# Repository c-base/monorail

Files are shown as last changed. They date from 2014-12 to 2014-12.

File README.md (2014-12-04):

monorail
========

Designfiles for Hardware and Electronics of the c-base monorail

#### Legende Dateinamen

Lo = Lokomotive (Traktionswagen)  
Kw = Kontrollwagen (Akku, Intelligenz..)  
Fw= Flaschenwagen  

Typ A# = Spant (Quer zur Fahrtrichtung, vertikal)  
Typ I# = Stringer (Längs zur Fahrtrichtung, paralell zur Schiene, vertikal oder schräg)  
Typ D# = Deck (Längs zur Fahrtrichtung, paralell zur Schiene, horizontale Oberfläche, Deck-ähnlich)  
Typ V# = Verstärkung / Aussteiffung  
Typ E# = Montagekomponente für Elektroteile  

lower caps u = "und" --> mehrere Komponenten in einer Datei

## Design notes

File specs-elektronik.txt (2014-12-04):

Anforderungen Elektronik Monorail

Modul "Abstand"
benötigt: pro Zug zwei
Anschlüsse:
	2x Bumper (links und rechts)
	1x IR-Distanz-sensor (sharp)
	1x RGB-LED (nicht extrem hell, aber auch keine müde funzel/kontroll-LED
	Bus
Stromversorgung vom Spannungsregler auf dem Akkucontrol-board

Modul "Motortreiber"
benötigt: pro Zug einen
	Anschluss des fertigen Motortreibers
	Bus
Stromversorgung vom Spannungsregler auf dem Akkucontrolboard
Motorstromversorgung direkt vom Akku mit vielen Volts

Modul "Akkucontrol"
benötigt: pro Zug einen
Anschlüsse:
	Akkustrom
	Ladestrom
	Balancerkontakte
	Bus
Funktionen:
	Laden und Balancen des Akkus
	Versorgung der Komponenten mit Strom in passender Spannung
		Bus-Strom: 3,3V
		Beagle bone black: 5V (vermutung!)
	Bereitstellung von Informationen über den Füllstand des Akkus über den Bus
	
Modul "Barcodescanner"
benötigt: pro Zug einen
Anschlüsse:
	IR-LED
	1-2 IR-Rx
	Bus
Stromversorgung vom Spannungsregler auf dem Akkucontrolboard
	
Modul "Flaschenwagen"
benötigt ersma gar nich, aber später pro Zug einen oder zwei
Anschlüsse:
	Modellbauservo oder kleiner Schrittmotor
	Lichtschranke oder Taster zum feststellen ob beladen oder leer
	LCD Display (zwei zeilen, z.b: http://www.watterott.com/de/Serial-Enabled-16x2-LCD-Yellow-on-Blue-5V
		dient zur Anzeige für wen die Ladung bestimmt ist, bzw was eingeladen werden soll durch den Barbot
	Bus
Stromversorgung direkt vom Akku für den Servo (7,5V). Der Mikrocontroller könnte entweder seinen eigenen Spannungsregler haben oder aber vom Akkucontrolboard mit versorgt werden
		
Modul "Lichtwagen"
benötigt: ersma gar nich, aber später irgendwann pro lichtzug einen
Anschlüsse:
	zwei Modellbauservos für X und Y Ausrichtung
	PWM-Steuerung für sehr starke LEDs (Strahler!)
	PWM-Steuerung für nen paar dekorative RGB-LEDs rund um den Lichtwagen
	Bus
Stromversorgung direkt vom Akku für die Servos und die Highpower-LEDs mit eigenem Spannungsregler. Der Mikrocontroller könnte entweder seinen eigenen Spannungsregler haben oder aber vom Akkucontrolboard mit versorgt werden
	
Modul "Kamerawagen"
benötigt: ersma gar nich, aber später irgendwann pro kamerazug einen
Anschlüsse:
	zwei Modellbauservos für X und Y Ausrichtung
	Stromversorgung für Kamera
	vll. remotesteuerung der kamera
	USB-Verbindung zum Beagleboneblack
Stromversorgung direkt vom Akku für den Kamerastrom mit Spannungsregler. Der Mikrocontroller könnte entweder seinen eigenen Spannungsregler haben oder aber vom Akkucontrolboard mit versorgt werden

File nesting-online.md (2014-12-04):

# Online Nesting Services

"Nesting" ist das automatisierte Anordnen von Formen auf 2D-Flächen zwecks maschineller Bearbeitung. Ein Lasercutter oder Wasserstrahljet soll möglichst wenig Verschnitt erzeugen und seine maximale Bearbeitungsfläche optimal ausnutzen. Nesting-Software erzeugt und optimiert die Anordnung vieler verschiedener Einzeilteile auf einer Fläche unter Berücksichtigung der benötigten Stückzahlen aller Einzelkomponenten.  

Nestingsoftware ist teuer, aber inzwischen gibt es auch Nesting-Dienstleister "in der Cloud". Hier sind zwei:

##### Nesting Online:  
http://www.e-nesting.com  
http://www.mynesting.com/

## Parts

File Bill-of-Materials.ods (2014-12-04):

BOM Monorail |  |  |  |  |  |  |  |  |  |  |  | Wegertseder Shop-Code: 645646-361
Name | Produktname | Bezeichnung | Abmessung | Stck/Gebinde | benötigte Menge | Gebindepreis | Einzelpreis | Gesamtpreis | Gebindemenge | Gebindegesamtpreis | alternativ shop mögl | ShopLink | Datenblatt | Anzahl übrig
Laufräder | Kugellager | FAG Rillenkugellager 626-2Z | 6x19x6 mm | 1 | 10 | 3,29 € | 3,29 € | 32,90 € | 10 | 32,90 € | nein | https://zahnriemen24.de/artikel_FAG-Rillenkugellager-626-2Z-6x19x6-mm__16_6_193 |  | 0
Radachse | Schraube | Zylinderschraube mit Innensechskant DIN 912 | 6x25mm | 20 | 12 | 2,45 € | 0,12 € | 1,47 € | 1 | 2,45 € | ja | Wegertseder 2534-430 |  | 8
Kupplung | Schraube | Zylinderschraube mit Innensechskant DIN 912 | 6x25 | 20 | 12 | 2,57 € | 0,13 € | 1,54 € | 1 | 2,57 € | ja | Wegertseder 2534-430 |  | 8
Verbindungschraube | Schraube | DIN 912 M6x 30 | 6x30 | 20 | 1 | 2,45 € | 0,12 € | 0,12 € | 1 | 2,45 € | ja | Wegertseder 2534-432 |  | 19
U-scheiben radlager | U-scheibe | DIN125 M6 U-Scheibe | 12x1,6 | 100 | 36 | 2,21 € | 0,02 € | 0,80 € | 1 | 2,21 € | ja | Wegertseder 1498-302 |  | 64
Radmutter | Mutter M6 | Selbstsichernde Mutter DIN 985 A2 M6 | 11,05x6mm | 100 | 12 | 3,47 € | 0,03 € | 0,42 € | 1 | 3,47 € | ja | Wegertseder 3346-238 |  | 88
Motor | NEMA17 | NEMA 17
Motormutter | Mutter | DIN125 M3 U-Scheibe |  | 200 | 10 | 2,14 € | 0,01 € | 0,11 € | 1 | 2,14 € | ja | Wegertseder 1498-294 |  | 190
Motorschrauben | M3x10 | DIN 6912 M3X10 |  | 25 | 6 | 1,84 € | 0,07 € | 0,44 € | 1 | 1,84 € | ja | Wegertseder 2534-280 |  | 19
IR-Sensor-Schraube | M3x30 | DIN912 M3 30mm | M3x30 | 25 | 4 | 3,14 € | 0,13 € | 0,50 € | 1 | 3,14 € | ja | Wegertseder 2534-296 |  | 21
IR-Sensor-Mutter | M3 | DIN985 A2 M3 |  | 100 | 4 | 3,45 € | 0,03 € | 0,14 € | 1 | 3,45 € | ja | Wegertseder 3346-232 |  | 96
Antriebslager | Kugellager | FAG Rillenkugellager 625-2Z (5x16x5 mm) | 5x16x5 mm | 1 | 6 | 3,39 € | 3,39 € | 20,34 € | 6 | 20,34 € | nein | https://zahnriemen24.de/artikel_FAG-Rillenkugellager-625-2Z-5x16x5-mm__16_6_191 |  | 0
Antriebsachse | Metallstange | Metallstange 5mm Durchmesser, 95mm länge | 5x95mm |  | 1 |  |  |  |  |  |  | Qshell
Antriebsrad |  | Druckteil Fablab
Zahnscheibe Motorachse |  | Zahnscheibe AL 16 T2,5/18-2 |  | 1 | 1 | 10,60 € | 10,60 € | 10,60 € | 1 | 10,60 € | nein | https://zahnriemen24.de/artikelno_10_1_835 |  | 0
Zahnscheibe Antriebsachse |  | Zahnscheibe AL 16 T2,5/36-2 |  | 1 | 1 | 12,05 € | 12,05 € | 12,05 € | 1 | 12,05 € | nein | https://zahnriemen24.de/artikel_Zahnscheibe-AL-16-T2,5-36-2__10_1_845 |  | 0
Antriebsriemen | Zahnriemen, geschlossen | PU-Zahnriemen 6-T2,5-200 | 200mmx6mm | 1 | 1 | 11,55 € | 11,55 € | 11,55 € | 1 | 11,55 € | nein | https://zahnriemen24.de/artikel_PU-Zahnriemen-6-T2,5-200__2_4_4863 |  | 0
Drehgestellgelenk | Gelenkkopf | Gelenkkopf mit Innengewinde M3 |  | 1 | 3 | 13,25 € | 13,25 € | 39,75 € | 3 | 39,75 € | jein | http://www.conrad.de/ce/de/product/216429/Gelenkkopf-mit-Innengewinde-M3-Stahl?ref=searchDetail | http://www.produktinfo.conrad.com/datenblaetter/200000-224999/216429-da-01-de-Gelenk_Gis_3.pdf | 0
Elektronik
Hauptcomputer | Beagle Bone Black |  | 88.98mm x 54.63mm x 18.84mm | 1 | 1 | 45,00 € | 45,00 € | 45,00 € | 1 | 45,00 € | nein | http://www.watterott.com/de/BeagleBone-Black |  | 0
Abstandssensor |  | Sharp GP2Y0A21YK0F |  | 1 | 2 | 9,15 € | 9,15 € | 18,30 € | 2 | 18,30 € | nein | http://www.watterott.com/de/Sharp-GP2Y0A21YK0F | http://www.watterott.com/index.php?page=product&info=995&dl_media=1326 | 0
Notstop-Bumper | Schnappschalter | Schnappschalter, 5A-250V~ Wechsler, Lötan. | 19,8x6,4x15,0 | 1 | 4 | 2,50 € | 2,50 € | 10,00 € | 4 | 10,00 € | nein | http://www.reichelt.de/Schnappschalter-Endschalter/MAR-1050-5202/3/index.html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 | http://www.reichelt.de/index.html?ACTION=7&LA=3&OPEN=0&INDEX=0 | 0
Motortreiber |  | DRV8825 Schrittmotortreiber (High Current) |  | 1 | 1 | 13,28 € | 13,28 € | 13,28 € | 1 | 13,28 € | ja | http://www.watterott.com/de/DRV8825-Stepper-Motor-Driver-Carrier-High-Current | http://www.pololu.com/file/download/drv8825.pdf?file_id=0J590 | 0
Laderaumantrieb | Turnigy TGY-4805 | Turnigy TGY-4805-1.5PA Sail Winch Servo (Drum Type) | Size: 40.3 x 20.3 x 38.7mm | 1 | 1 | 8,28 € | 8,28 € | 8,28 € | 1 | 8,28 € |  | http://www.hobbyking.com/hobbyking/store/__42638__Turnigy_TGY_4805_1_5PA_Sail_Winch_Servo_Drum_Type_.html | http://84.200.30.165/cosmoshop/lshopimage/a/HIT-112081/zn1/HIT-112081_n1.jpg | 0
Laderaumverriegelung | Micro-Servo | HKSCM12-5 Single Chip Digital Servo (5V) 10g / 1.5kg / 0.18s |  | 1 | 2 | 2,91 € | 2,91 € | 5,82 € | 2 | 5,82 € | ja | http://www.hobbyking.com/hobbyking/store/__16261__HKSCM12_5_Single_Chip_Digital_Servo_5V_10g_1_5kg_0_18s.html | http://www.produktinfo.conrad.com/datenblaetter/500000-524999/507765-da-01-de-HUBMAGNET_HMB_1513_001_12VDC.pdf | 0
Akku |  | SLS XTRON 3200mAh 4S1P 14,8V 20C/40C | LxBxH 138x43x26mm | 1 | 1 | 33,99 € | 33,99 € | 33,99 € | 1 | 33,99 € | ja | http://www.stefansliposhop.de/liposhop/SLS-XTRON/SLS-XTRON-20C/SLS-XTRON-3200mAh-4S1P-14-8V-20C-40C::978.html |  | 0
Display |  | ST7565 Positive GLCD (128x64) with RGB backlight |  | 1 | 1 | 17,09 € | 17,09 € | 17,09 € | 1 | 17,09 € |  | http://www.watterott.com/de/ST7565-Positive-GLCD-128x64-with-RGB-backlight
Werkzeug und Schienen
Blindnietmutterzange |  |  |  | 1 | 1 | 27,99 € | 27,99 € | 27,99 € | 1 | 27,99 € | ja | http://www.amazon.de/Nietmaschine-Nietmuttern-Popnietzange-Nietzange-Einnietmutter/dp/B00A0280H8 |  | 0
Blindnietmutter |  | alu nietmutter m3x0,5 |  | 100 | 100 | 13,99 € | 0,14 € | 13,99 € | 1 | 13,99 € | ja | http://www.amazon.de/stk-Alu-Nietmutter-Nietmuttern-Blindnietmuttern/dp/B00AY01JXS |  | 0
rohrbiegegerät |  |  |  | 1 | 1 | 44,99 € | 44,99 € | 44,99 € | 1 | 44,99 € | ja | http://www.amazon.de/Hand-Rohrbieger-Rohre-Rohrbiegegerät-Kupfer-Bieger/dp/B00BIWCMKU |  | 0
Muttern |  | DIN 985 M3 A2 |  | 100 | 100 | 2,00 € | 0,02 € | 2,00 € | 1 | 2,00 € | ja | http://www.amazon.de/100-Stück-Edelstahl-Sechskantmuttern-selbstsichernd/dp/B004QV5EOQ |  | 0
Gewindestange |  | M3 x 1000mm V2A DIN975 | 3x1000 | 1 | 2 | 1,50 € | 1,50 € | 3,00 € | 2 | 3,00 € | ja | http://www.amazon.de/Stück-1000mm-Edelstahl-V2A-Gewindestange/dp/B004YE8ASW |  | 0
SchienenBohrer |  | Ironside 230114 HSS-Bohrer 5,0mm 2St.G DIN338 RN-geschliffen | 5mm | 2 | 2 | 4,85 € | 2,43 € | 4,85 € | 1 | 4,85 € | ja | http://www.amazon.de/Ironside-230114-HSS-Bohrer-DIN338-RN-geschliffen/dp/B0001E36I8?s=diy |  | 0
Schiene |  | 22 x 1 mm 2,5 m | 22x1x2500mm | 2,5 | 5 | 13,50 € | 5,40 € | 27,00 € | 2 | 27,00 € |  | http://www.hornbach.de/shop/Kupferrohr-als-Stange-22-x-1-mm-2-5-m/1318872/artikel.html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 |  | 0
Zahnriemen |  | Zahnriemen 10 -T10 - 3000 - offen - kevlar | 3000mm lang 10mm breit | 3 | 1 | 21,40 € | 7,13 € | 7,13 € | 1 | 21,40 € |  |  |  | 2
 |  |  |  |  |  |  |  | Gesamtpreis |  | Gebindegesamtpreis
SUMME |  |  |  |  |  |  |  | 415,44 € |  | 447,89 €
 |  |  |  |  |  |  |  |  |  | Preis für das zweite Fahrzeug
 |  |  |  |  |  |  |  |  |  | 280,42 €
 |  |  |  |  | Schienenpreis
 |  |  |  |  | Breite holzbalken |  |  | 30
 |  |  |  |  | höhe holzbalken |  |  | 40
 |  |  |  |  | Montageabstand |  |  | 25
 |  |  |  |  | Zugabe länge |  |  | 15
 |  |  |  |  | abstand zw halterung |  |  | 500
 |  |  |  |  | Länge Gewindestange |  |  | 80
 |  |  |  |  | Bedarf pro Meter |  |  | 160
 |  |  |  |  | Kosten Gewindestange |  |  | 0,24 €
 |  |  |  |  | Menge Muttern pro Meter |  |  | 6 | 0,21 €
 |  |  |  |  | Menge U-Scheiben pro Meter |  |  | 6 | 0,06 €
 |  |  |  |  | Kosten pro Meter |  |  | 5,91 €
 |  |  |  |  | Kosten pro Meter mit zahnschiene |  |  | 13,04 €

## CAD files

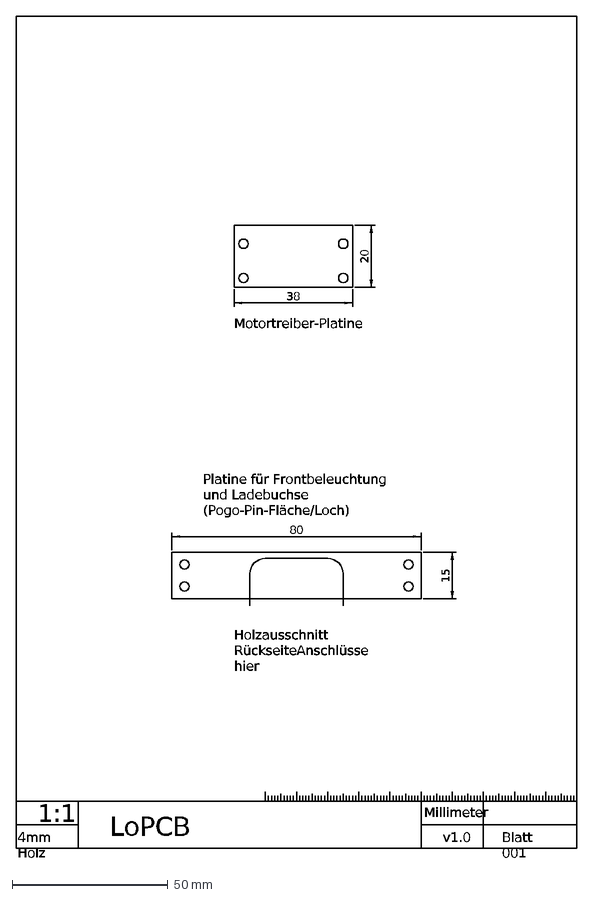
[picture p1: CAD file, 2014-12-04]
LoPCB.dxf
1:1
4mm Holz
Blatt 001
v1.0
Millimeter
Platine für Frontbeleuchtung und Ladebuchse (Pogo-Pin-Fläche/Loch)
Holzausschnitt Rückseite Anschlüsse hier
Motortreiber-Platine
LoPCB
38
20
80
15

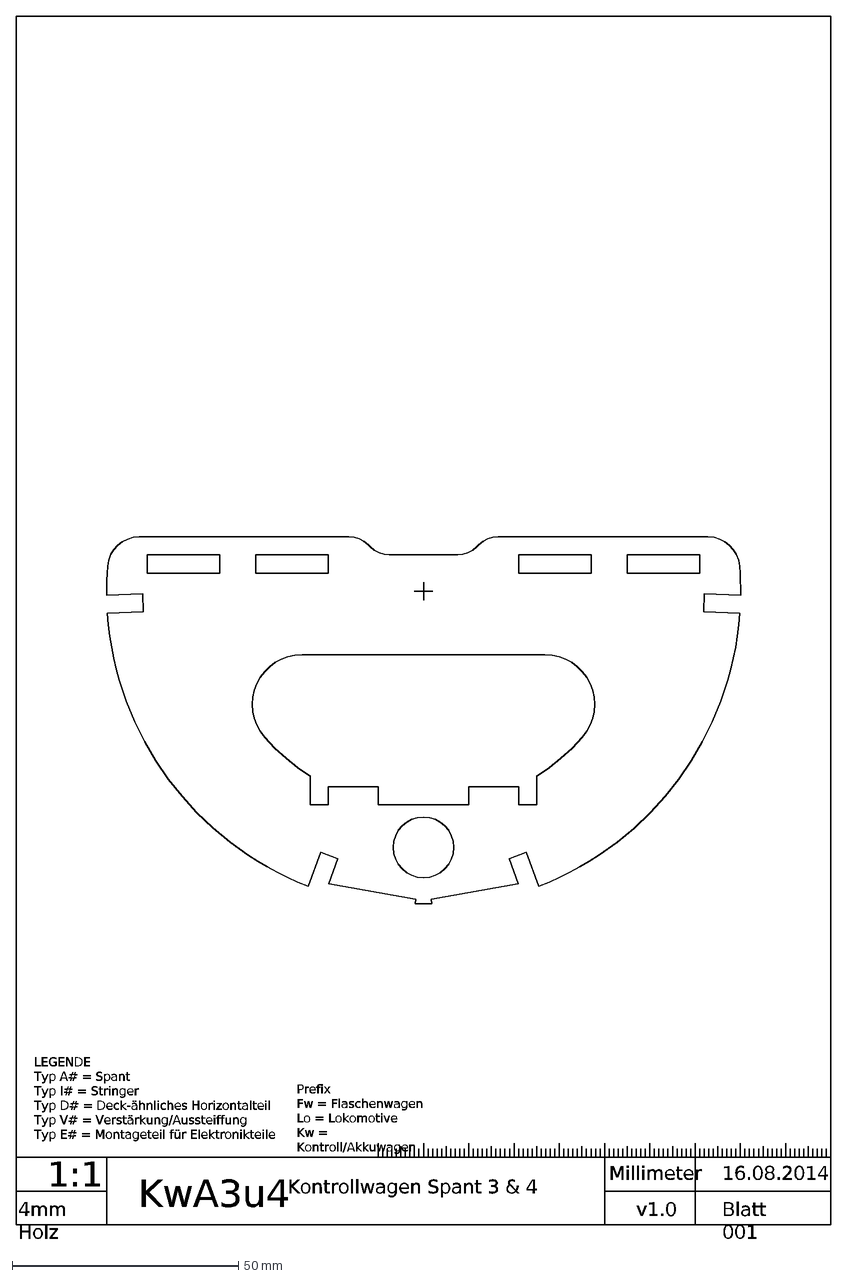
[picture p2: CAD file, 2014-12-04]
KwA3u4.dxf
1:1
4mm Holz
16.08.2014
Blatt 001
v1.0
Millimeter
LEGENDE Typ A# = Spant Typ I# = Stringer Typ D# = Deck-ähnliches Horizontalteil Typ V# = Verstärkung/Aussteiffung Typ E# = Montageteil für Elektronikteile
Prefix Fw = Flaschenwagen Lo = Lokomotive Kw = Kontroll/Akkuwagen
Kontrollwagen Spant 3 & 4
KwA3u4

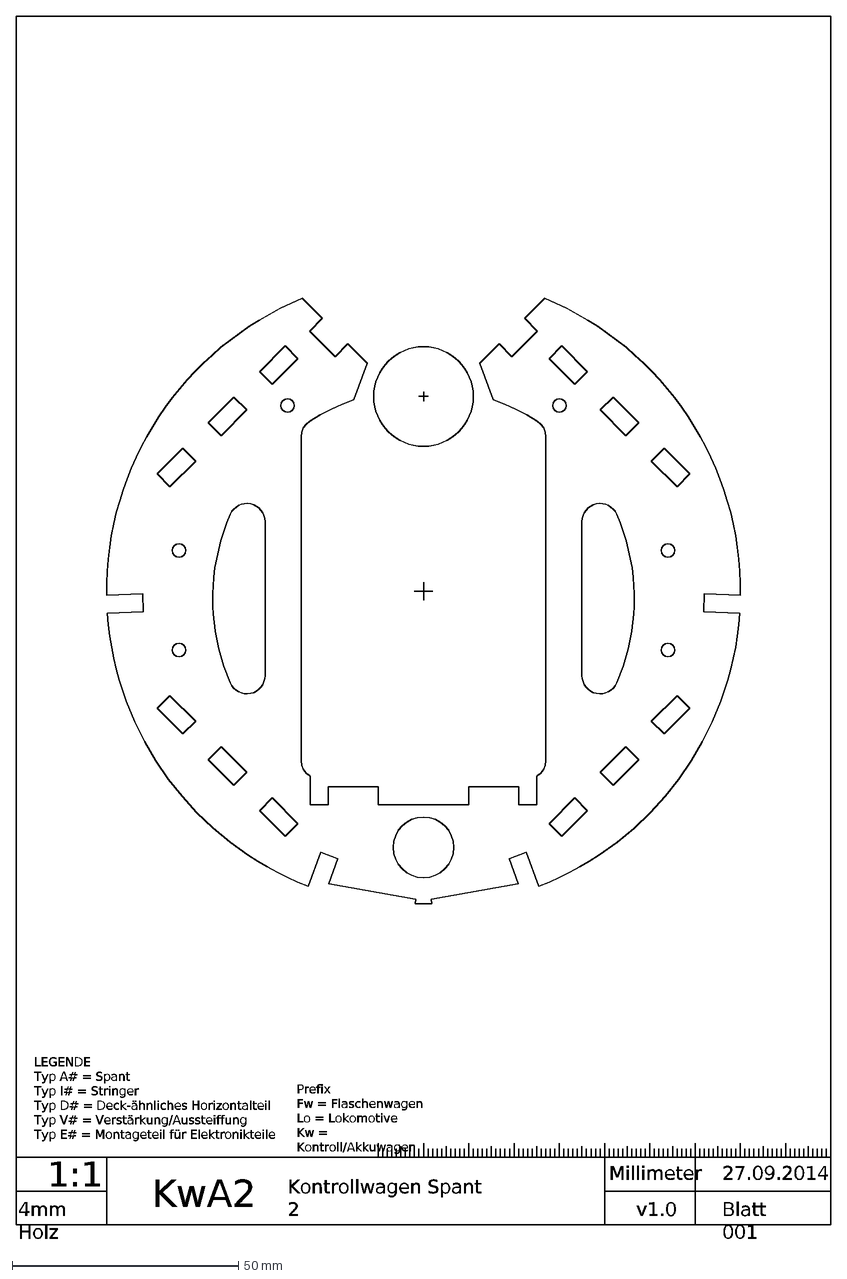
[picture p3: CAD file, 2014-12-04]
KwA2.dxf
1:1
4mm Holz
Blatt 001
v1.0
Millimeter
LEGENDE Typ A# = Spant Typ I# = Stringer Typ D# = Deck-ähnliches Horizontalteil Typ V# = Verstärkung/Aussteiffung Typ E# = Montageteil für Elektronikteile
Prefix Fw = Flaschenwagen Lo = Lokomotive Kw = Kontroll/Akkuwagen
KwA2
Kontrollwagen Spant 2
27.09.2014

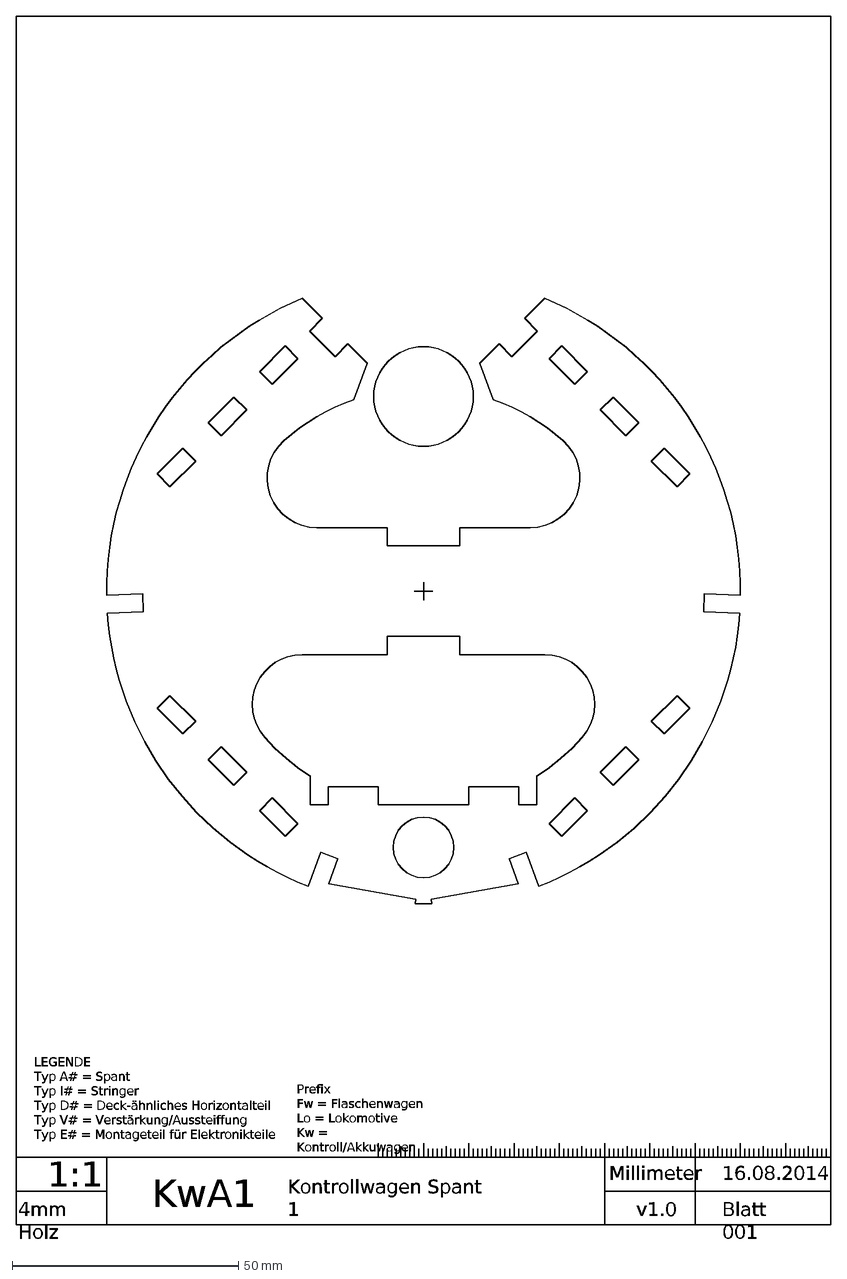
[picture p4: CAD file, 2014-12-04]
KwA1.dxf
1:1
4mm Holz
16.08.2014
Blatt 001
v1.0
Millimeter
LEGENDE Typ A# = Spant Typ I# = Stringer Typ D# = Deck-ähnliches Horizontalteil Typ V# = Verstärkung/Aussteiffung Typ E# = Montageteil für Elektronikteile
Prefix Fw = Flaschenwagen Lo = Lokomotive Kw = Kontroll/Akkuwagen
KwA1
Kontrollwagen Spant 1

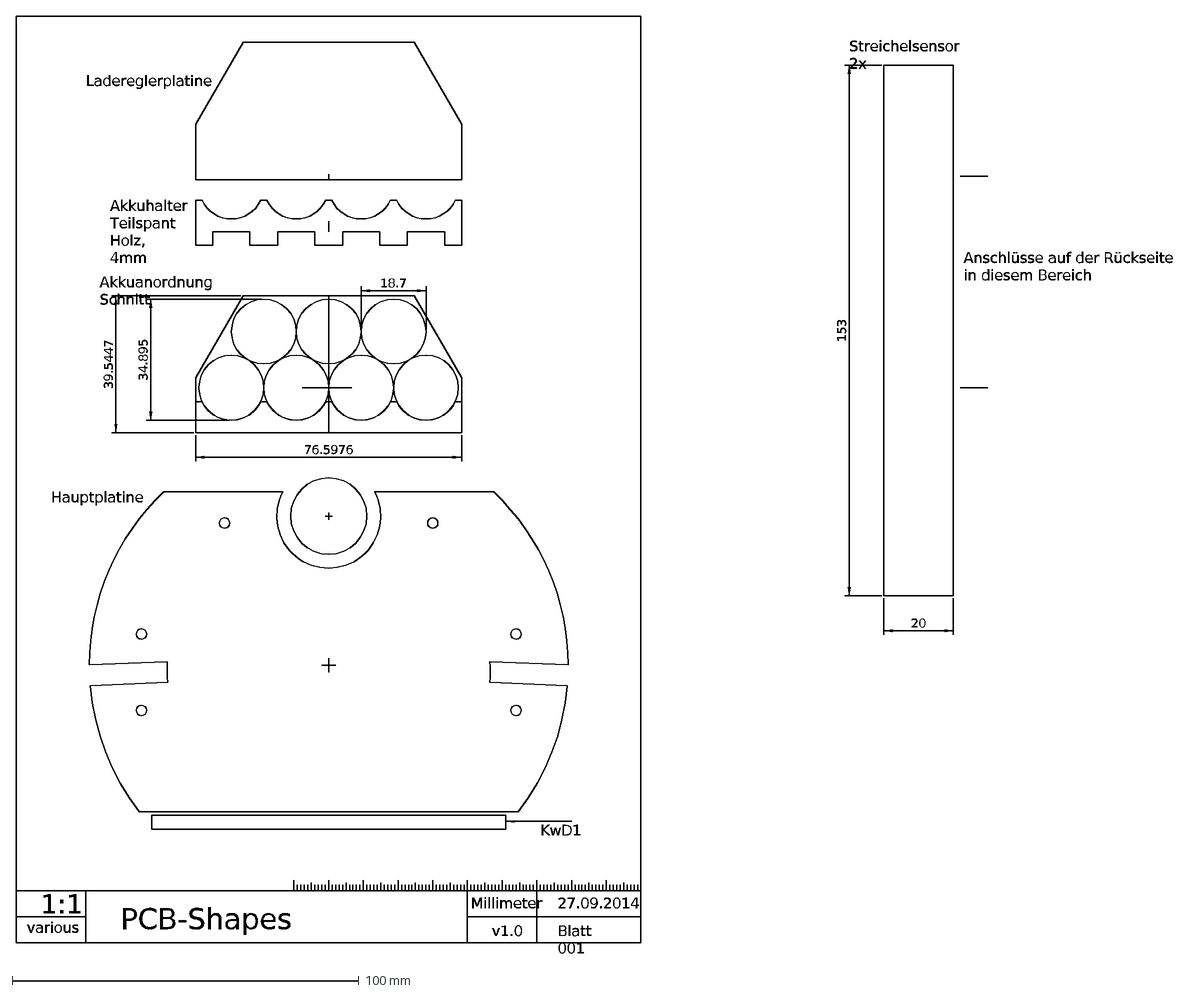
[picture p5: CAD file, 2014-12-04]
KwPCB.dxf
1:1
Blatt 001
v1.0
Millimeter
34.895
76.5976
18.7
39.5447
Ladereglerplatine
Akkuhalter Teilspant
Hauptplatine
PCB-Shapes
27.09.2014
KwD1
Holz, 4mm
various
Akkuanordnung Schnitt
Streichelsensor 2x
Anschlüsse auf der Rückseite in diesem Bereich
153
20

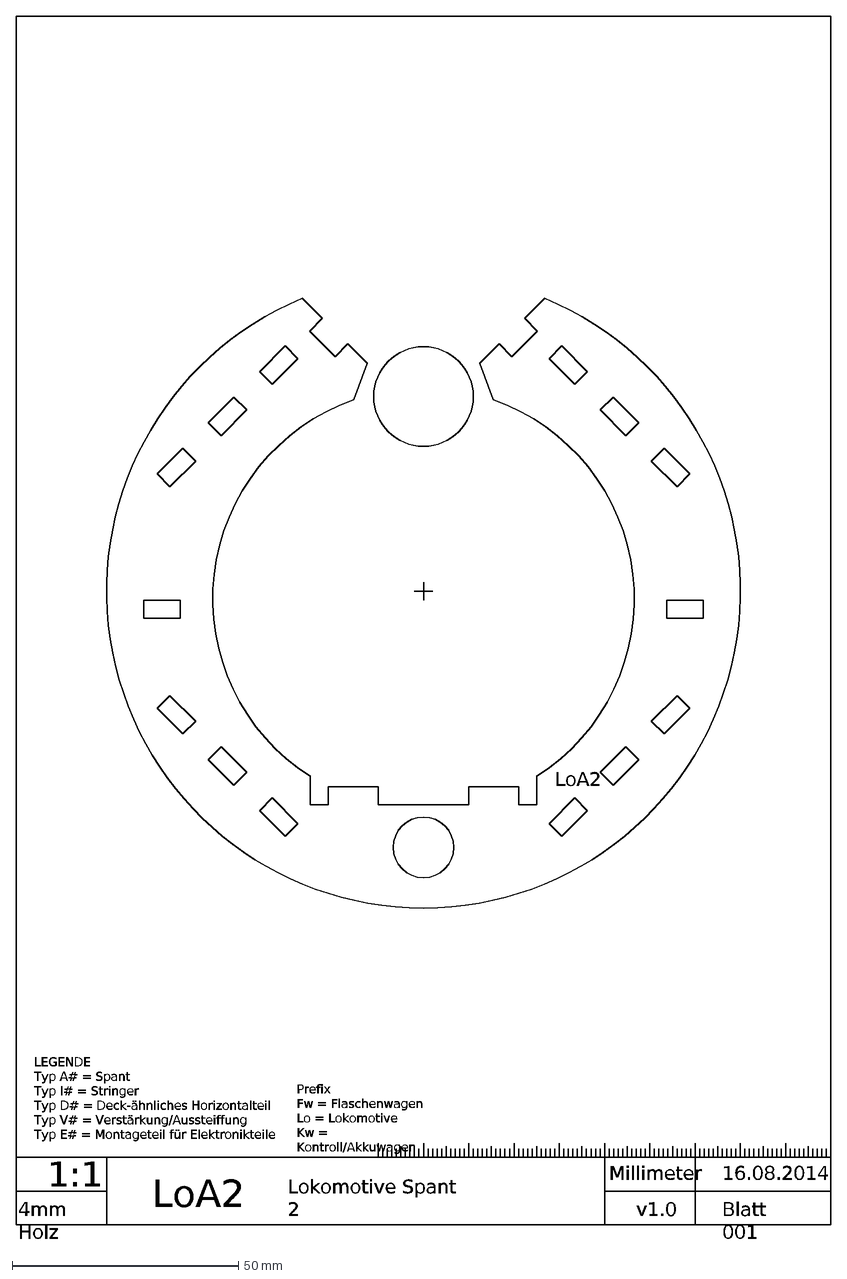
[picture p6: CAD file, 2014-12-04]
LoA2.dxf
1:1
4mm Holz
16.08.2014
Blatt 001
v1.0
Millimeter
LEGENDE Typ A# = Spant Typ I# = Stringer Typ D# = Deck-ähnliches Horizontalteil Typ V# = Verstärkung/Aussteiffung Typ E# = Montageteil für Elektronikteile
Prefix Fw = Flaschenwagen Lo = Lokomotive Kw = Kontroll/Akkuwagen
Lokomotive Spant 2
LoA2

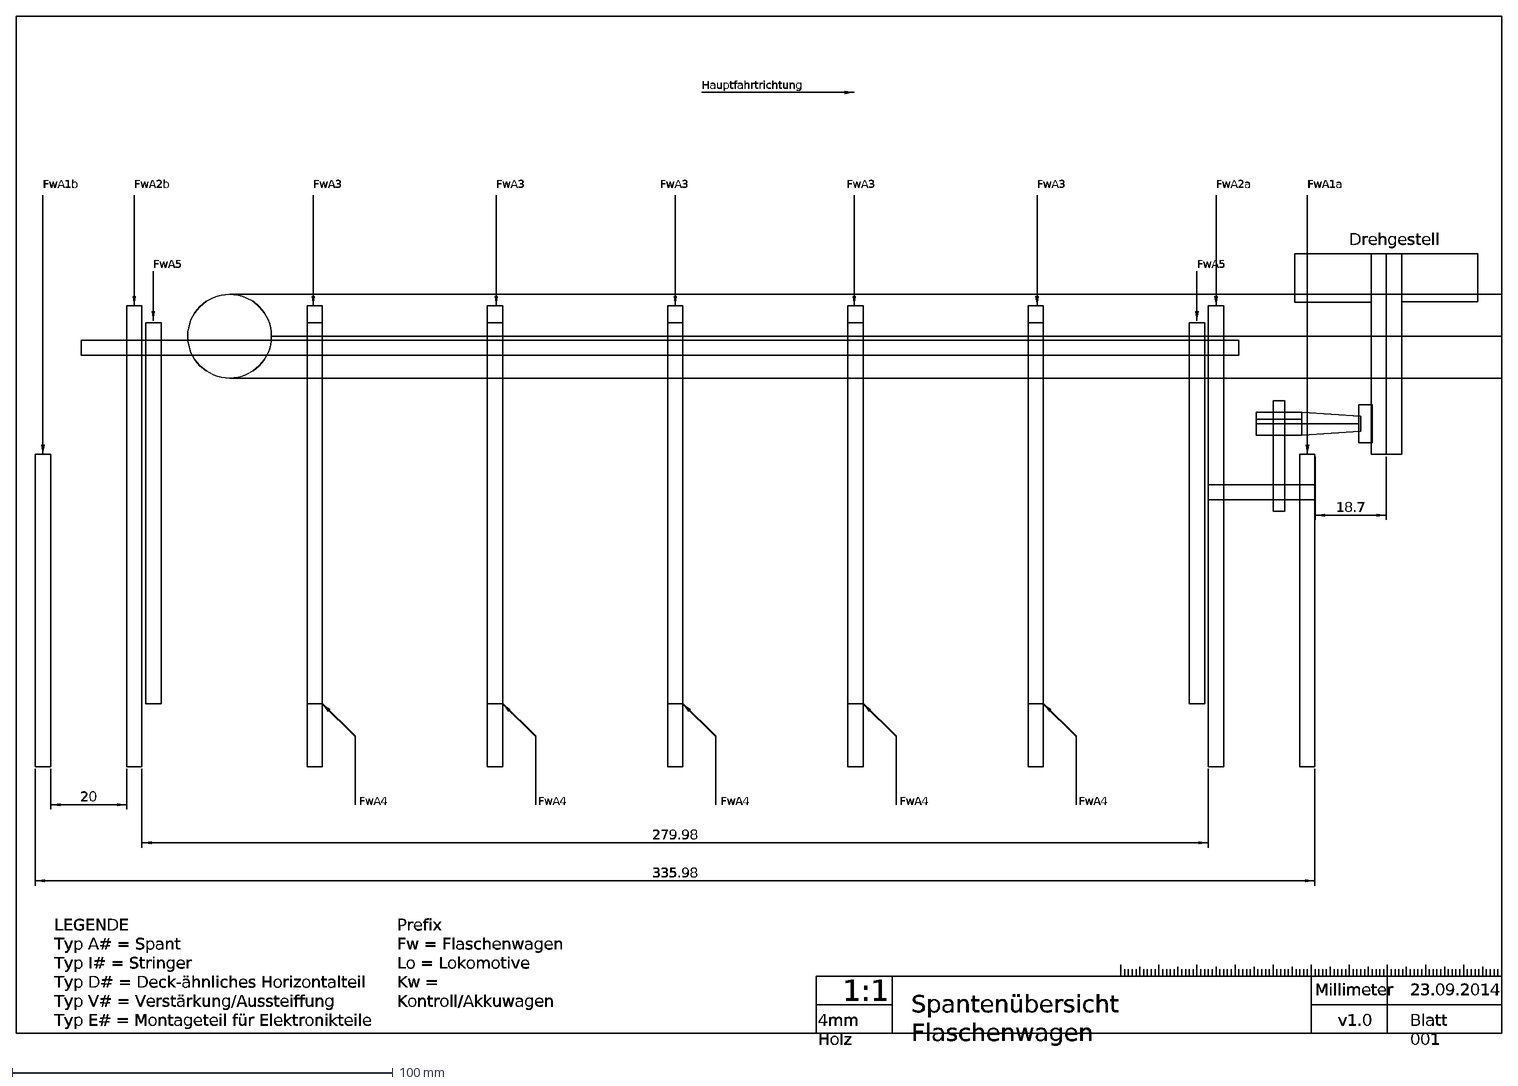
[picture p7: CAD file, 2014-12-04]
Fw-A-Spantenübersicht.dxf
1:1
4mm Holz
Blatt 001
v1.0
279.98
335.98
20
Spantenübersicht Flaschenwagen
Drehgestell
18.7
LEGENDE Typ A# = Spant Typ I# = Stringer Typ D# = Deck-ähnliches Horizontalteil Typ V# = Verstärkung/Aussteiffung Typ E# = Montageteil für Elektronikteile
Prefix Fw = Flaschenwagen Lo = Lokomotive Kw = Kontroll/Akkuwagen
Hauptfahrtrichtung
FwA3
FwA4
Millimeter
FwA5
FwA1a
FwA1b
FwA2a
FwA2b
23.09.2014

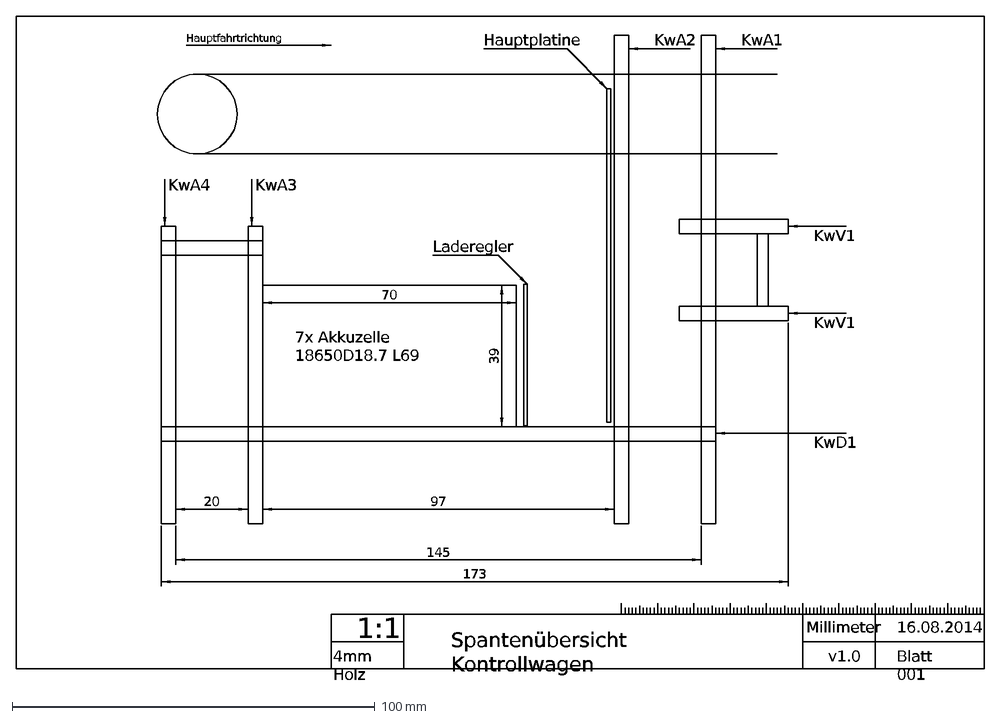
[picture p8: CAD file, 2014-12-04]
Kw-A-Spantenübersicht.dxf
1:1
4mm Holz
16.08.2014
Blatt 001
v1.0
Millimeter
Spantenübersicht Kontrollwagen
145
KwA1
KwA2
KwA3
KwA4
KwV1
KwD1
70
39
Laderegler
Hauptplatine
7x Akkuzelle 18650 D18.7 L69
Hauptfahrtrichtung
20
97
173

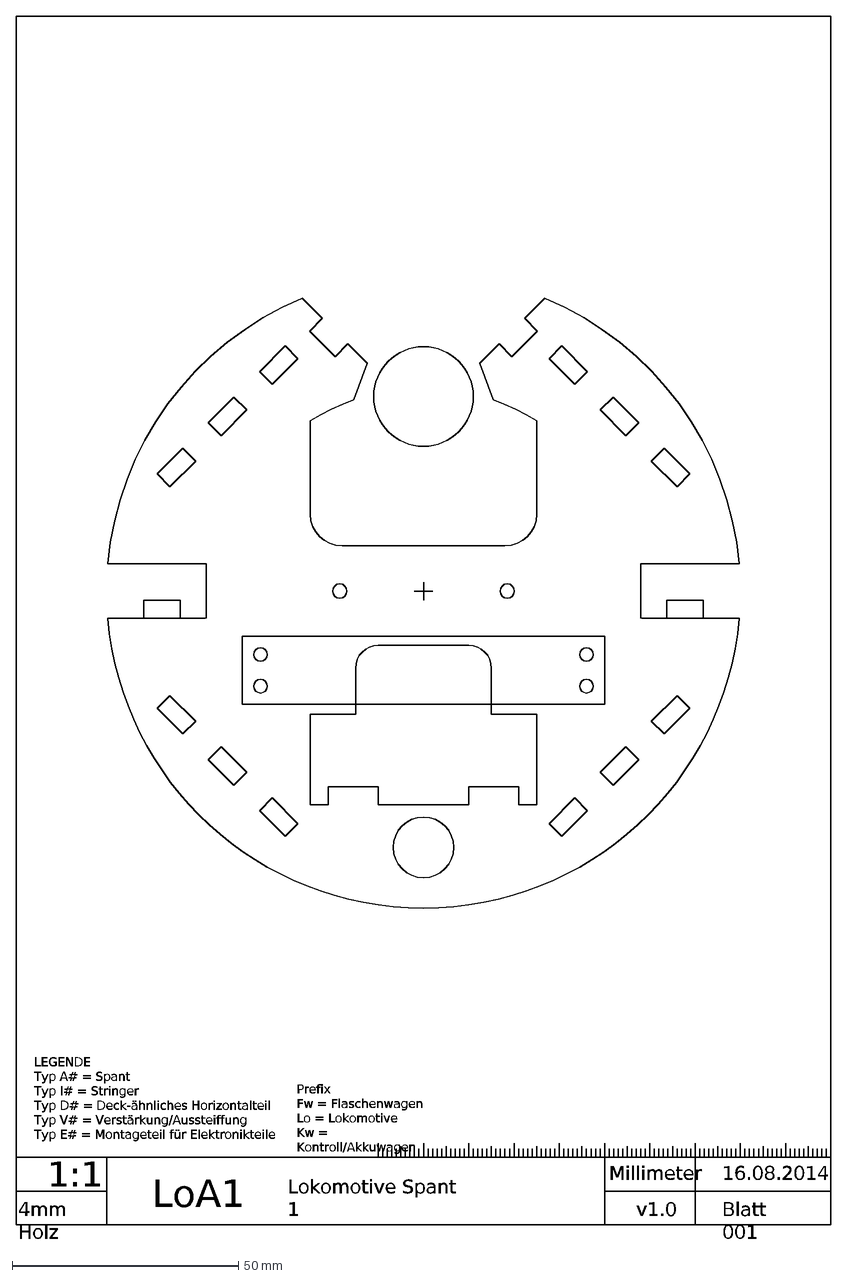
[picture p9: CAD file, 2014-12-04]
LoA1.dxf
1:1
4mm Holz
16.08.2014
Blatt 001
v1.0
Millimeter
LoA1
LEGENDE Typ A# = Spant Typ I# = Stringer Typ D# = Deck-ähnliches Horizontalteil Typ V# = Verstärkung/Aussteiffung Typ E# = Montageteil für Elektronikteile
Prefix Fw = Flaschenwagen Lo = Lokomotive Kw = Kontroll/Akkuwagen
Lokomotive Spant 1

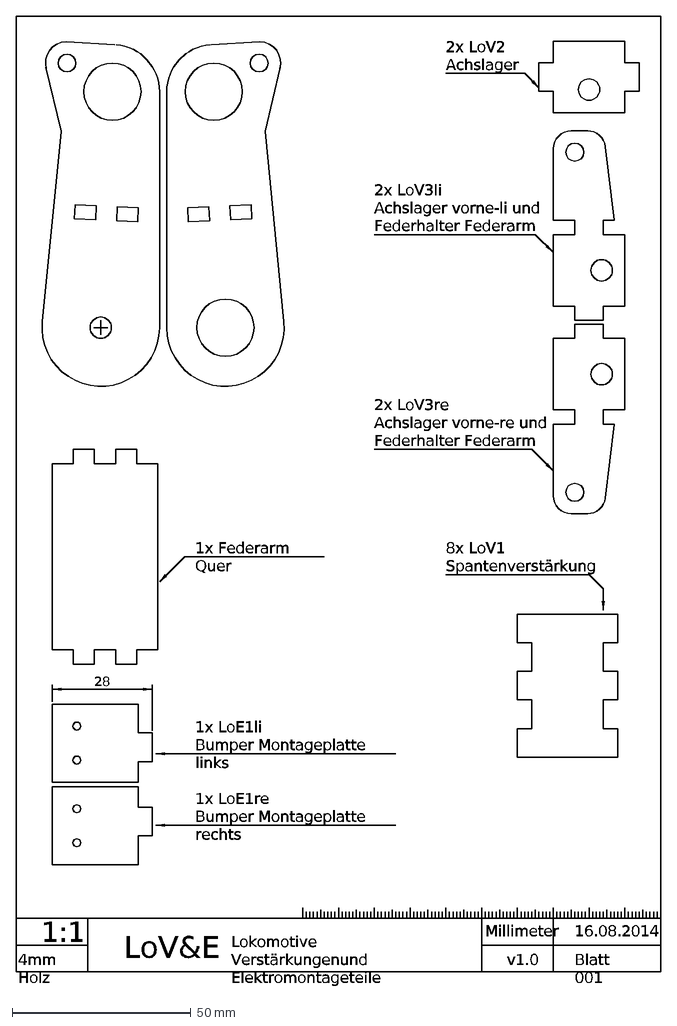
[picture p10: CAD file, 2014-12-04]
LoVE.dxf
1:1
4mm Holz
16.08.2014
Blatt 001
v1.0
Millimeter
Lokomotive Verstärkungen und Elektromontageteile
1x Federarm Quer
1x LoE1li Bumper Montageplatte links
1x LoE1re Bumper Montageplatte rechts
8x LoV1 Spantenverstärkung
2x LoV2 Achslager
2x LoV3li Achslager vorne-li und Federhalter Federarm
2x LoV3re Achslager vorne-re und Federhalter Federarm
LoV&E
28

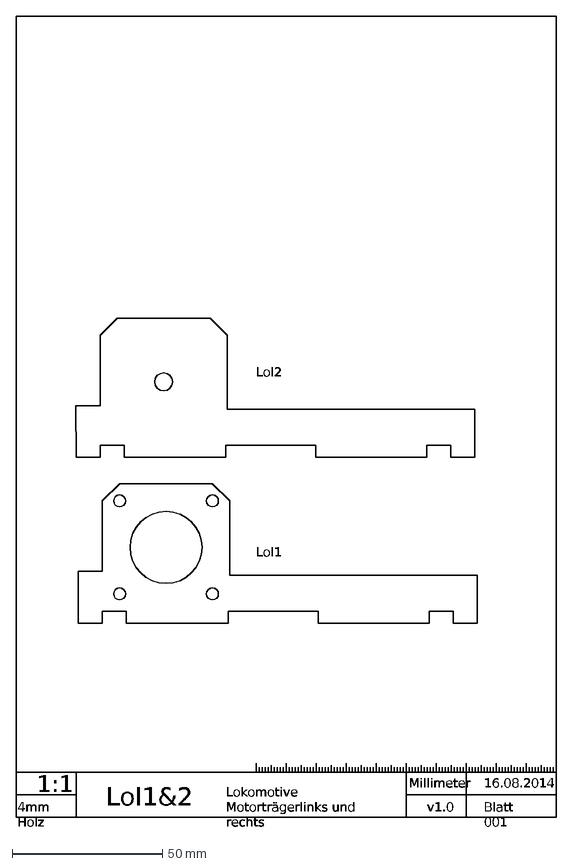
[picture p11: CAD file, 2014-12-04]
LoI1u2.dxf
1:1
4mm Holz
16.08.2014
Blatt 001
v1.0
Millimeter
LoI1&2
Lokomotive Motorträger links und rechts
LoI1
LoI2

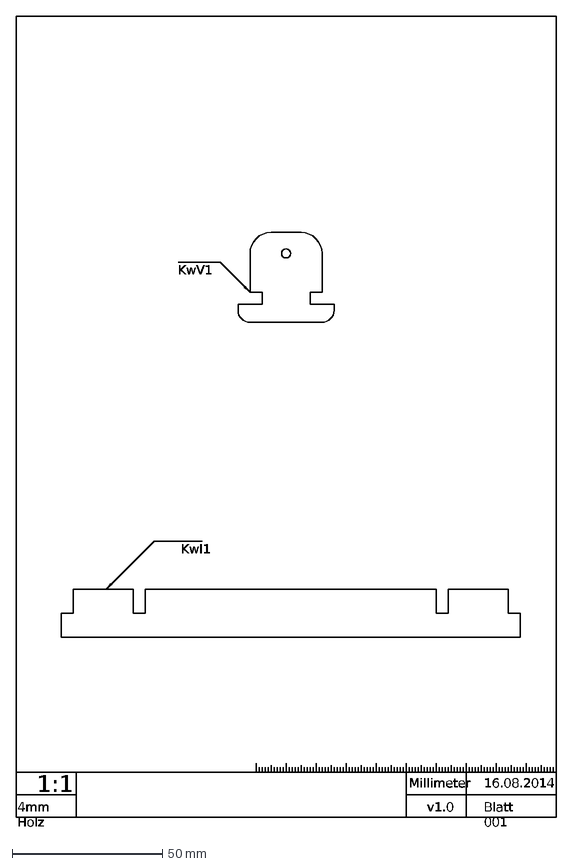
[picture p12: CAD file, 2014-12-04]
KwIuV.dxf
1:1
4mm Holz
16.08.2014
Blatt 001
v1.0
Millimeter
KwI1
KwV1

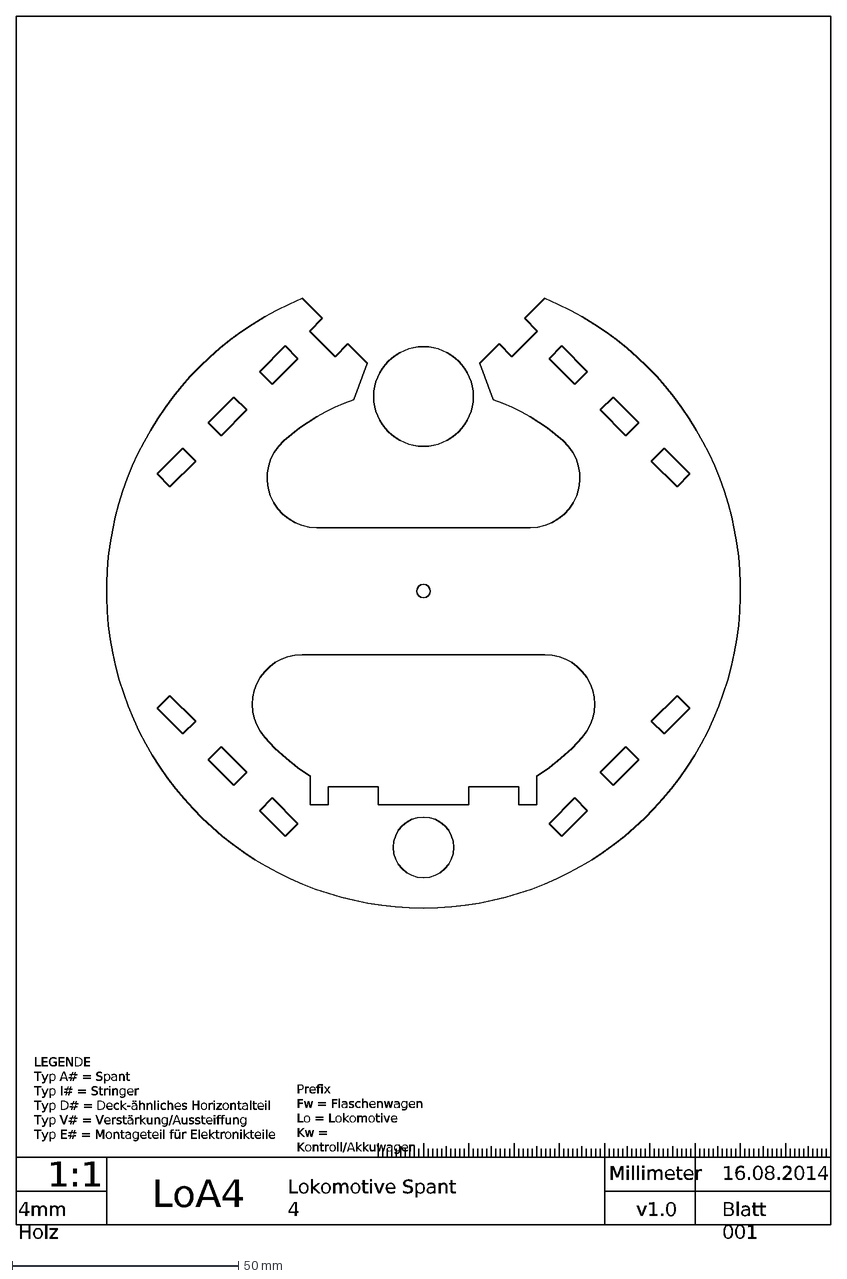
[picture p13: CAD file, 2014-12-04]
LoA4.dxf
1:1
4mm Holz
16.08.2014
Blatt 001
v1.0
Millimeter
LEGENDE Typ A# = Spant Typ I# = Stringer Typ D# = Deck-ähnliches Horizontalteil Typ V# = Verstärkung/Aussteiffung Typ E# = Montageteil für Elektronikteile
Prefix Fw = Flaschenwagen Lo = Lokomotive Kw = Kontroll/Akkuwagen
Lokomotive Spant 4
LoA4

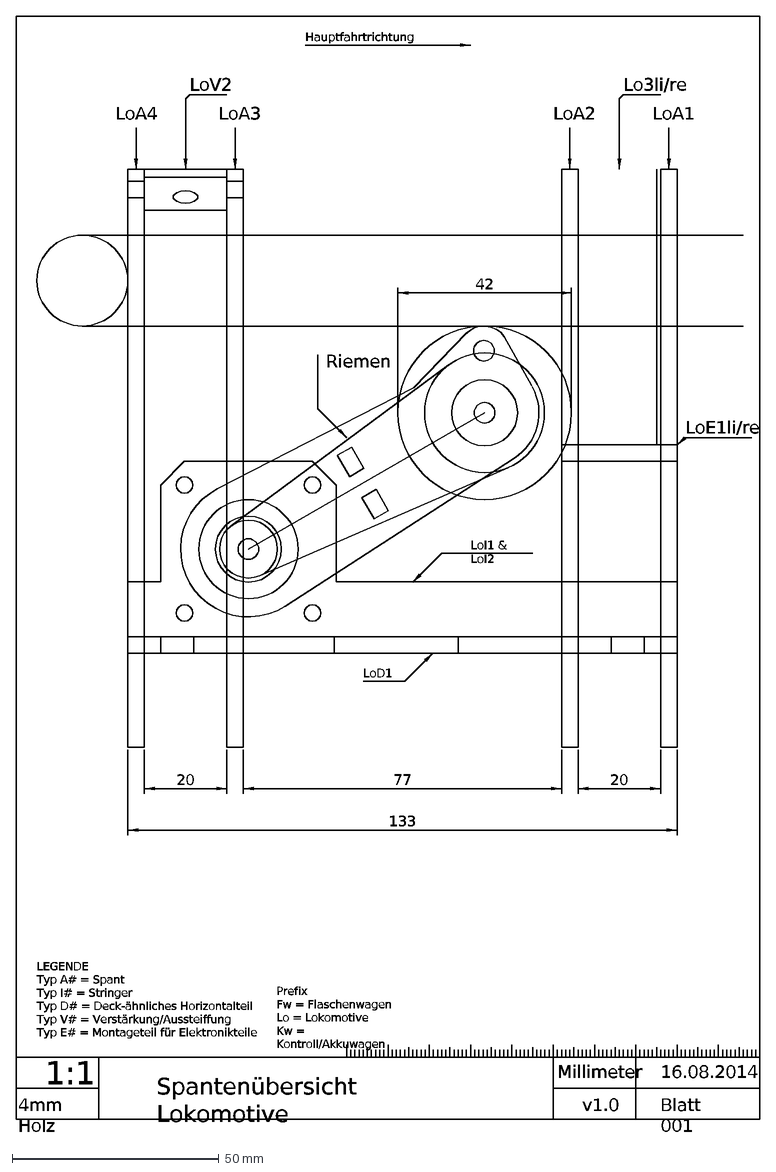
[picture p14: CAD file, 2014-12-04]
Lo-A-Spantenübersicht.dxf
1:1
4mm Holz
16.08.2014
Blatt 001
v1.0
Spantenübersicht Lokomotive
133
42
Riemen
LEGENDE Typ A# = Spant Typ I# = Stringer Typ D# = Deck-ähnliches Horizontalteil Typ V# = Verstärkung/Aussteiffung Typ E# = Montageteil für Elektronikteile
LoA1
LoA2
LoA3
LoA4
Hauptfahrtrichtung
LoI1 & LoI2
LoD1
20
77
Millimeter
Prefix Fw = Flaschenwagen Lo = Lokomotive Kw = Kontroll/Akkuwagen
LoV2
Lo3li/re
LoE1li/re

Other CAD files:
template-empty-plans.dxf
Robolab-Teststrecke.dxf
Prellbock-Ladegerät.dxf
LoD1.dxf
Fw-S-Profilübersicht.dxf
KwD1.dxf
LoA3.dxf

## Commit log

2014-12-04 init. 18 monate entwicklung und schon gibts den ersten push!
    [Bill-of-Materials.ods, Fw-A-Spantenübersicht.dxf, Fw-S-Profilübersicht.dxf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]
2014-12-04 bisschen mehr angaben und erklärung
2014-12-04 Streichelsensoren-Ausschnitte zum KwA# hinzugefügt
    [KwA1.dxf, KwA2.dxf, KwA3u4.dxf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]
